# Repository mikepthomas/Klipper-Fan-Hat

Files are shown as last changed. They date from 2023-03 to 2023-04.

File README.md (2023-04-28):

# Klipper Fan Hat

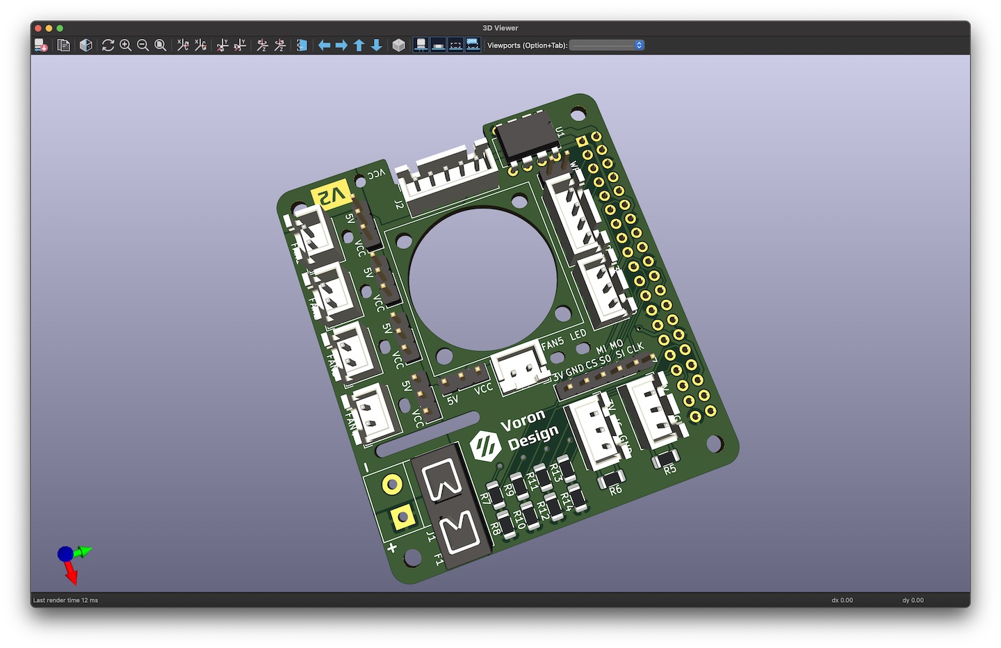
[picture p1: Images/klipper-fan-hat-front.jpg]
Klipper Fan Hat Front


[Interactive bom](https://mikethomas.info/Klipper-Fan-Hat)

### A Hat to use with the [Raspberry Pi as a Secondary MCU in Klipper](https://www.klipper3d.org/RPi_microcontroller.html):
- SKR Pico compatible input for powering the Pi and Serial communication
- 5 Mosfet outputs (with 2 pin JST-XH connectors standard on most fans used on 3D printers)
- Voltage selector jumpers to power each fan from either 5V or VCC supplied by screw terminal
- I2C and 1-Wire and SPI headers for connecting accesories to the Raspberry Pi
- 2 headers connected to General Purpose GPIO pins for accesories such as Filament Run Out Sensors

### Documentation

[Documentation and Setup information here](Documentation/README.md)

 Parts that I sourced for assembly:
- 1206 Capacitor Set [Ali Express](https://www.aliexpress.com/item/1005002907508304.html)
- 1206 LEDs [Ali Express](https://www.aliexpress.com/item/1005003836509392.html)
- 1206 Resistor Set [Ali Express](https://www.aliexpress.com/item/33029877427.html)
- 2510 Axial Fan [Ali Express](https://www.aliexpress.com/item/32807610078.html)
- Blade Fuse Holder [Ali Express](https://www.aliexpress.com/item/1005003194700697.html)
- DIP-8 24C32 EEPROM [Ali Express](https://www.aliexpress.com/item/33036366759.html)
- DIP-8 Socket [Ali Express](https://www.aliexpress.com/item/1005001650813894.html)
- IRLML6344TRPBF Mosfets [Ali Express](https://www.aliexpress.com/item/1005004711783484.html)
- JST-XH Connector Set [Ali Express](https://www.aliexpress.com/item/33000442968.html)
- Jumper Caps [Ali Express](https://www.aliexpress.com/item/1005004482029258.html)
- KF301 Screw Terminal [Ali Express](https://www.aliexpress.com/item/1005003311688833.html)
- M2.5x14 BHCS [Ali Express](https://www.aliexpress.com/item/1005004123548619.html)
- Pin Header Set [Amazon](https://www.amazon.co.uk/gp/product/B07CWSXY7P)
- Raspberry Pi Headers and Spacers [Amazon](https://www.amazon.co.uk/gp/product/B07PHBTTGV)

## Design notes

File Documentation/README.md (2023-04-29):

- [Components](#components)
  - [Indicator LEDs](#indicator-leds)
  - [Power In](#power-in)
  - [Serial Header](#serial-header)
  - [I2C Header](#i2c-header)
  - [1-wire Header](#1-wire-header)
  - [GPIO Header](#gpio-header)
  - [SPI Header](#spi-header)
  - [Fan Mosfets](#fan-mosfets)
- [Setup](#setup)

# Components

## Indicator LEDs

There are 7 status indicator LEDs on the board:

- Status LED to indicate that the board is communicating with Klipper (LED)
- VCC status indicates that there is power present on the Vin and GND feeding the board through the screw terminals (J1)
- 5 Fan Status LEDs to indicate if the Fan Mosfets have power applied to them (FAN1-FAN5)

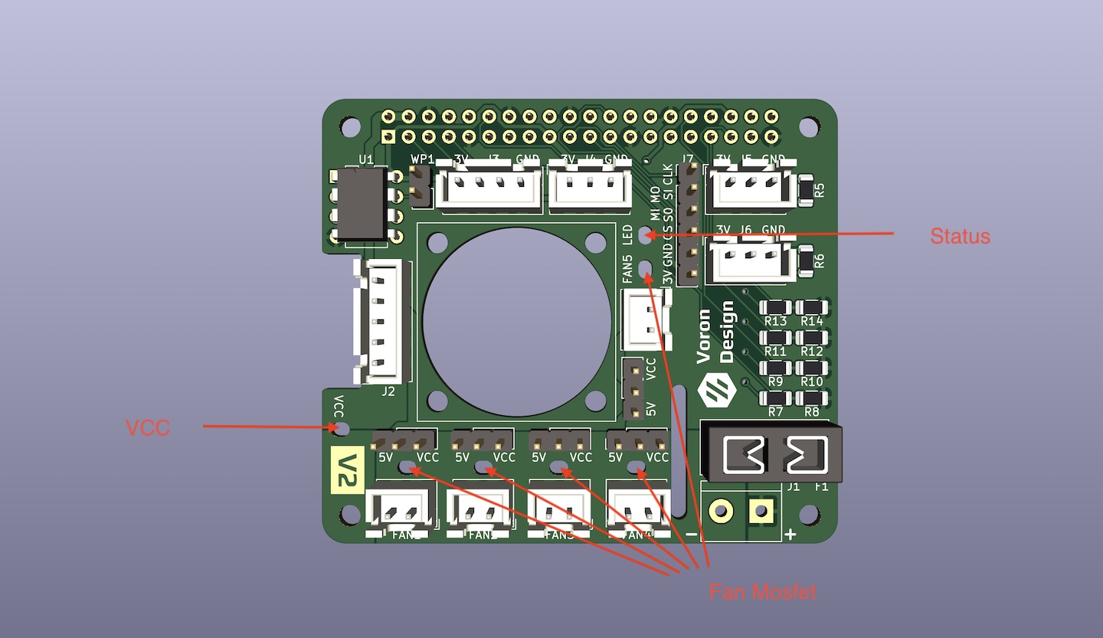
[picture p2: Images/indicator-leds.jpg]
Indicator LEDs


The Status LED is connected directly to GPIO16 with a current limiting resistor.

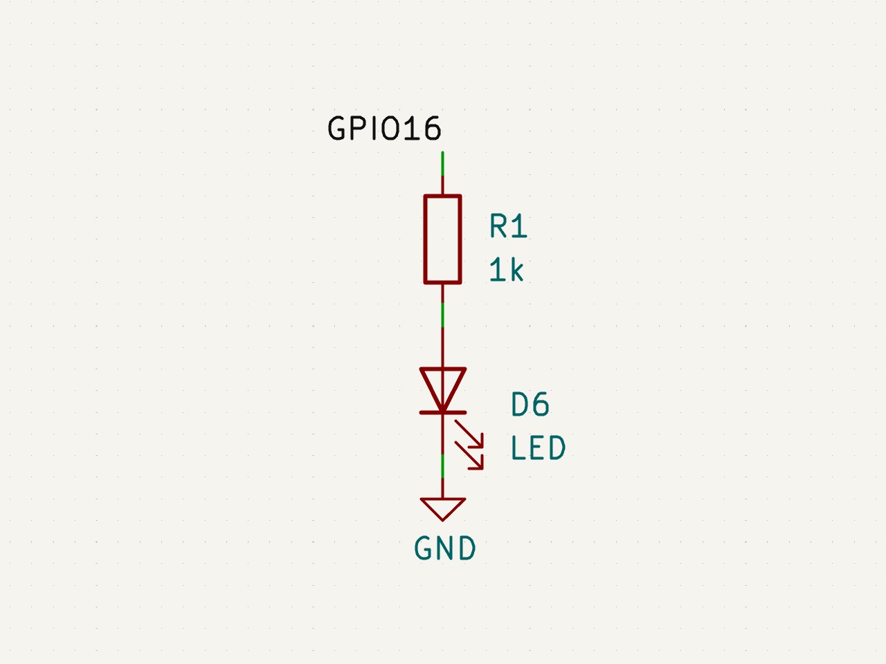
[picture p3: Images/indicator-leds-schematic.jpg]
Indicator LEDs Schematic


Example klipper ready status configuration:

```bash
[static_digital_output status_led]
pins: rpi:gpio16
```

## Power In

VCC and GND are for feeding power to the Mosfets, this would typically be either 12V or 24V.

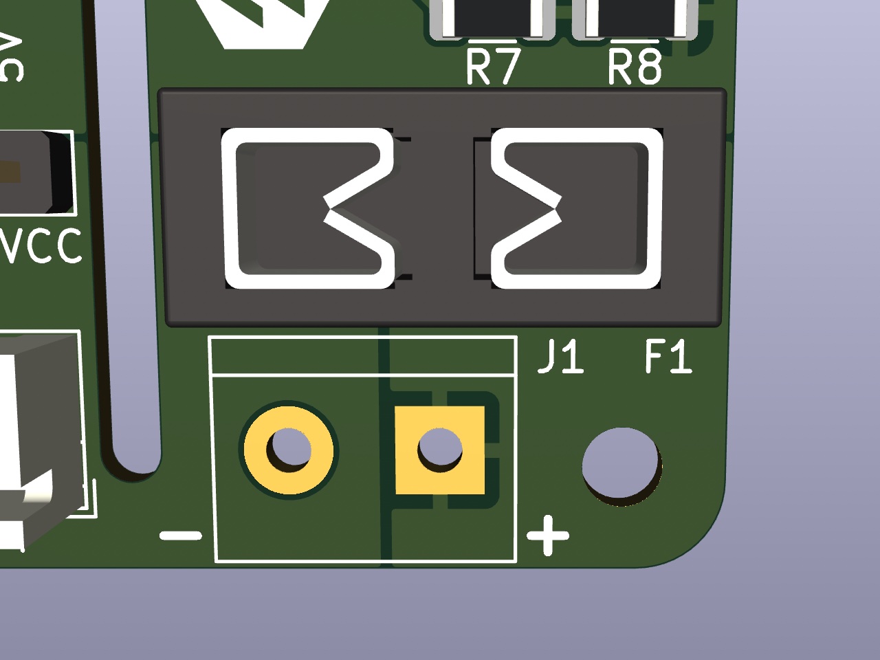
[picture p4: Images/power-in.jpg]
Power In


The fuse is a micro blade type fuse and should be chosen to the maximum draw of all of the MOSFET fed devices.

For example, if you are running a 40W heater, 2 5W fans and 1 2W fan, you will need a total of 62W of power. At 24V, this would translate to 62W/24V = 2.58A. The closest fuse might be a 5A fuse, which you should use.

Maximum power should not exceed 12A as the MOSFETs are each rated to a maximum of 3A.

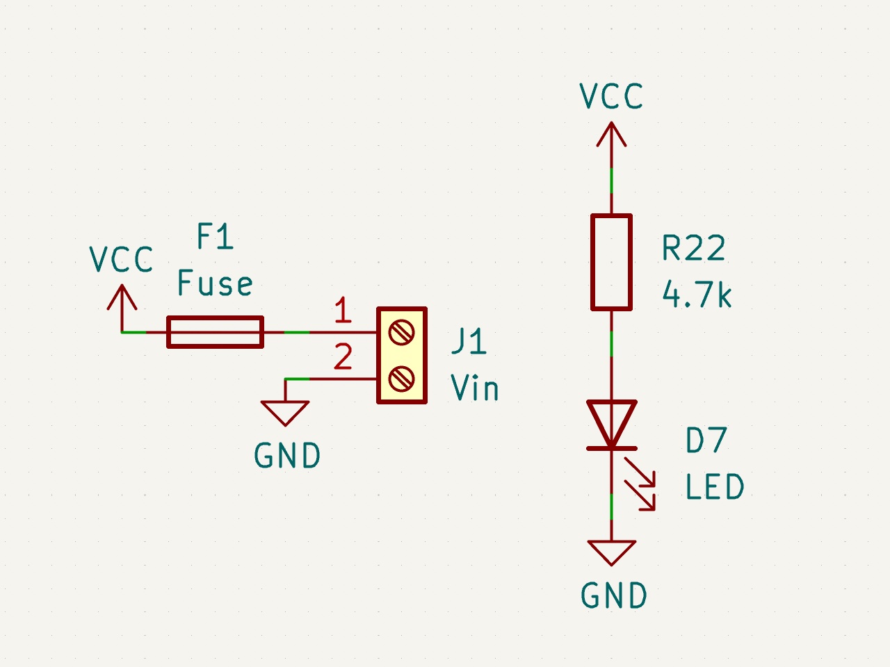
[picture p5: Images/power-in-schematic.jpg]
Power In Schematic


## Serial Header

SKR Pico compatible interface, can be used to both power the Raspberry Pi and communicate with the MCU over Serial.

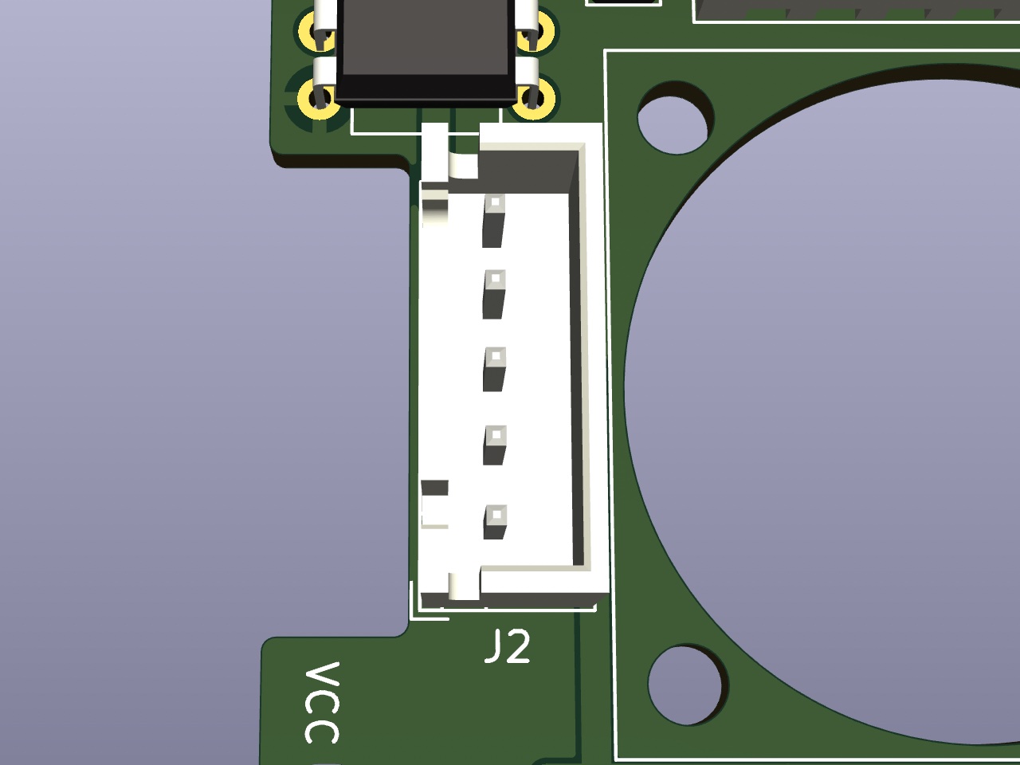
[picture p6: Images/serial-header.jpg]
Serial Header


The 5V pins are connected directly to the Raspberry Pi 5V pins and also supply 5V to the mosfet power selector headers.

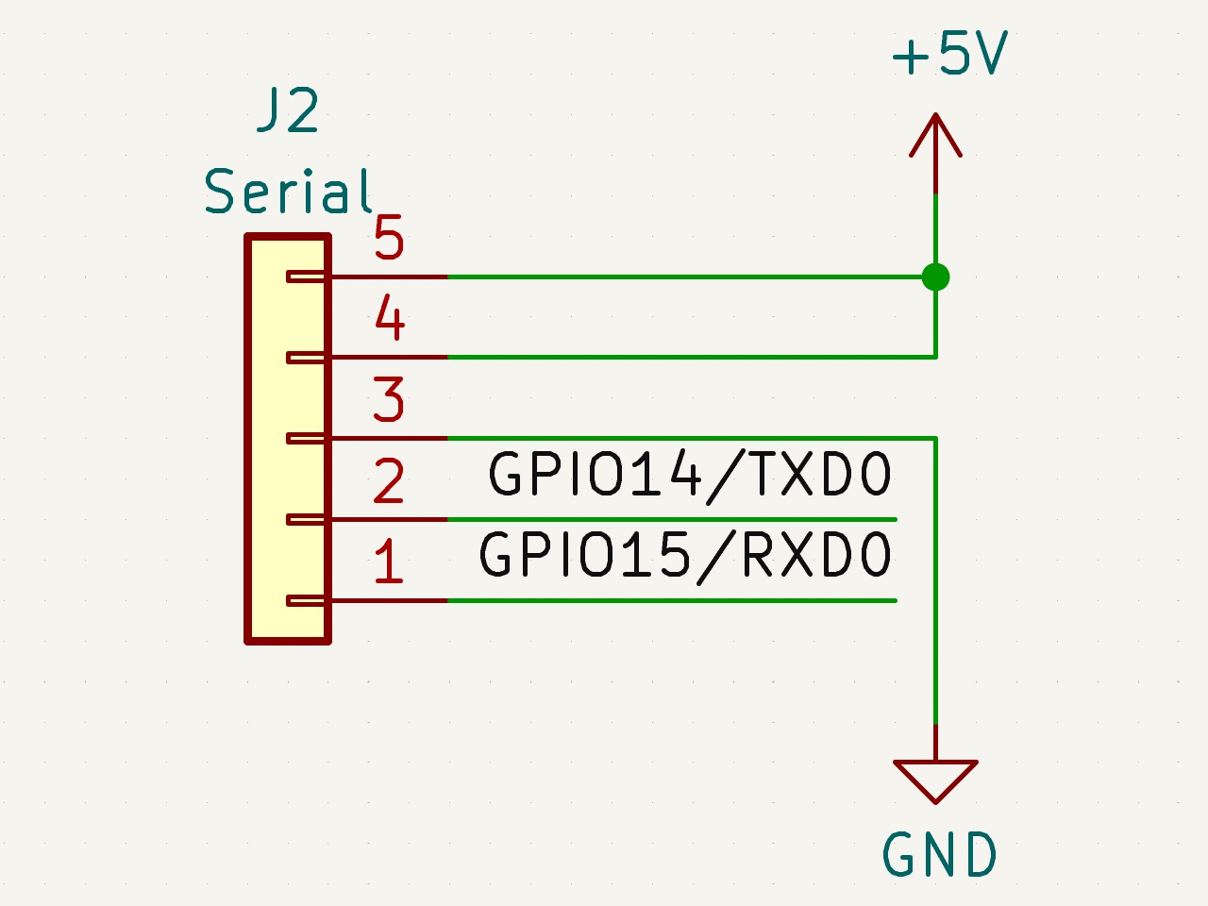
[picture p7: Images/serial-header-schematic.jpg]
Serial Header Schematic


## I2C Header

Contains a 3.3V I2C bus for connecting displays, and other sensors such as environemntal sensors and breakout expanders. This plugs into J3.

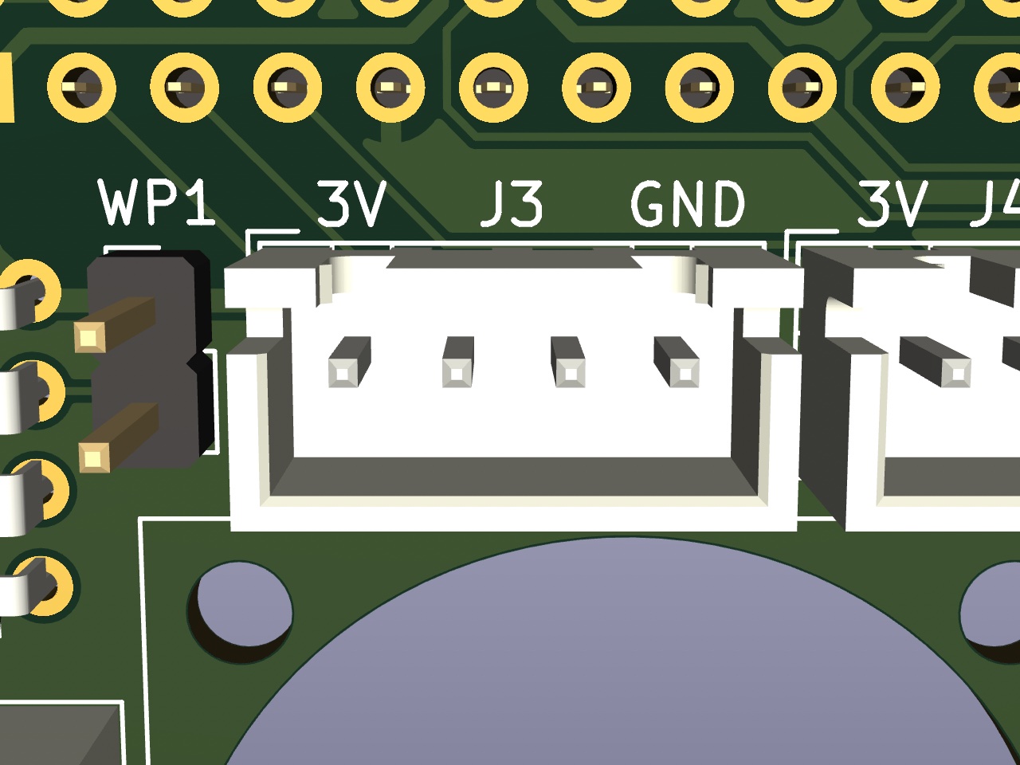
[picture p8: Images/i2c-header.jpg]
I2C Header


There are no Pull Up resistors on the I2C Bus as the Raspberry Pi already includes them.

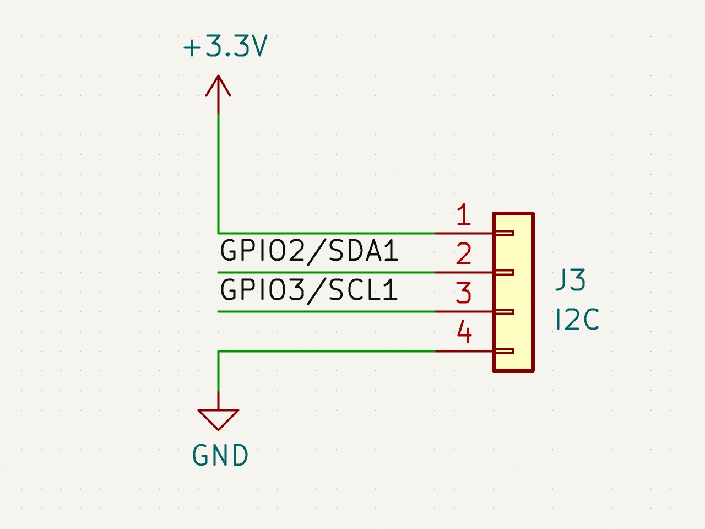
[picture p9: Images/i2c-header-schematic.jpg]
I2C Header Schematic


Example display configuration:

```bash
[display]
lcd_type: sh1106
i2c_mcu: rpi
i2c_bus: i2c.1
```

Example HTU21D temperature sensor configuration:

```bash
[temperature_sensor enclosure_temp]
sensor_type: HTU21D
i2c_mcu: rpi
i2c_bus: i2c.1

[gcode_macro QUERY_ENCLOSURE]
gcode:
    {% set sensor = printer["htu21d enclosure_temp"] %}
    {action_respond_info(
        "Temperature: %.2f C\n"
        "Humidity: %.2f%%" % (
            sensor.temperature,
            sensor.humidity))}
```

## 1-wire Header

The 1-wire connector can be used for connecting 1-wire sensors or can also be used as another generic GPIO Header.

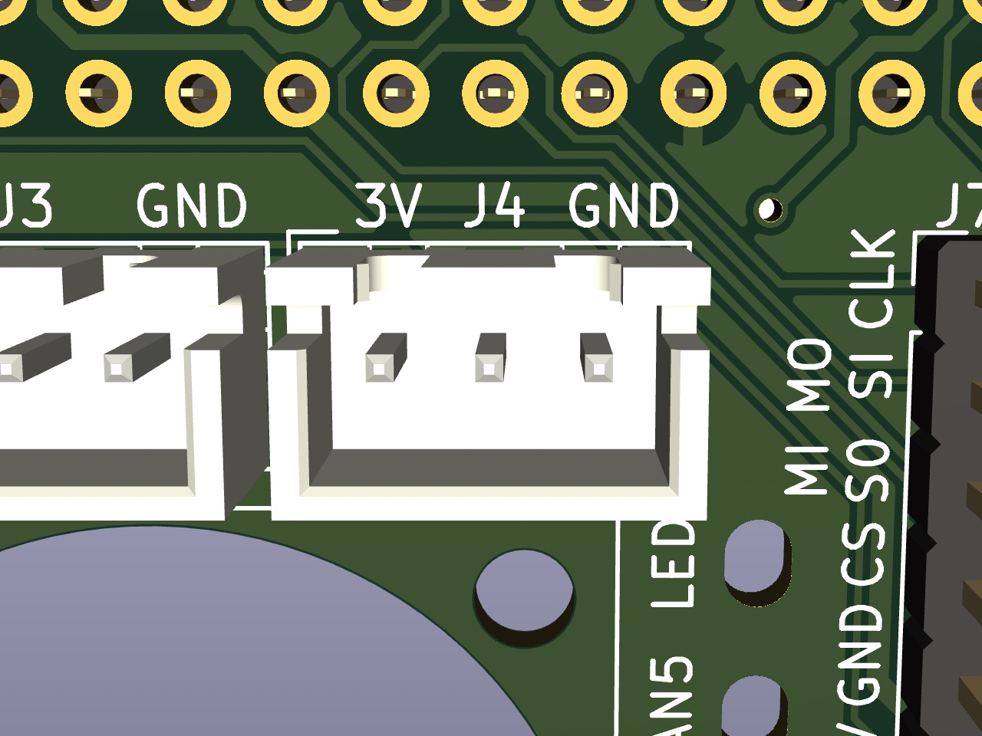
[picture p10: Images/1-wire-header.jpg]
1-wire Header


The 1-wire pin, GPIO4 is pulled up to 3V3 with a 3.9k resistor.

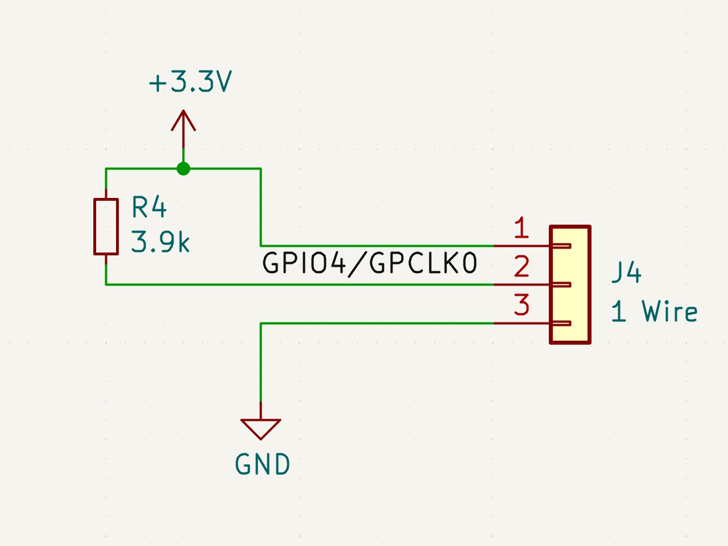
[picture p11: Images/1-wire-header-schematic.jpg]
1-wire Header Schematic


Example Output Pin configuration:

```bash
[output_pin gpio4]
pin: rpi:gpio4
value: 0
shutdown_value: 0
```

Example DS18B20 temperature sensor configuration:

```bash
[temperature_sensor enclosure_temp]
sensor_type: DS18B20
serial_no: 28-031674b175ff # Find with: ls /sys/bus/w1/devices/
ds18_report_time: 3.0 # Seconds between readings, minimum of 1.0
sensor_mcu: rpi
```

## GPIO Header

The GPIO headers J4 and J5 (3V3, GPIO, GND) is available for creative uses.

Examples of what this can be used for include adding external mosfets, relays or a filament runout sensors.

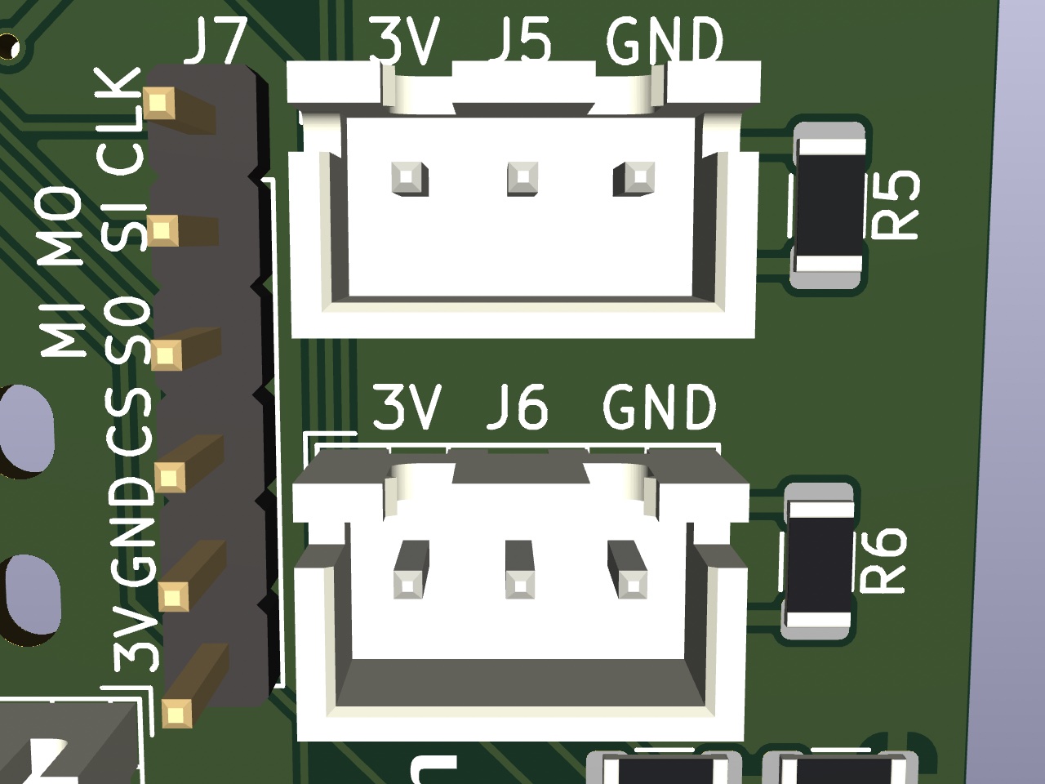
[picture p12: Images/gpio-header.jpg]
GPIO Header


Both GPIO5 and GPIO6 pins are pulled up to 3V3 with a 3.9k resistor.

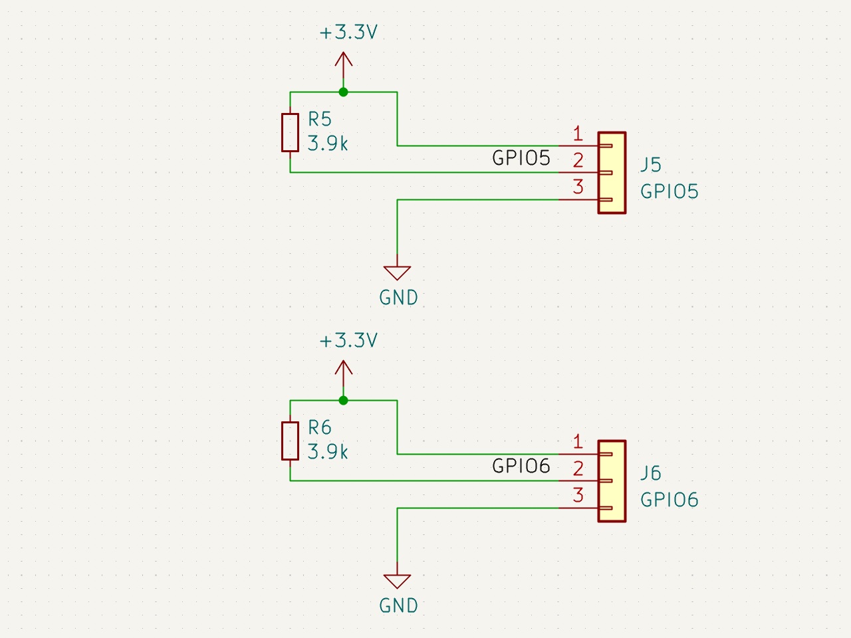
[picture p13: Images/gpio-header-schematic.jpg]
GPIO Header Schematic


Example Output Pin configuration:

```bash
[output_pin gpio5]
pin: rpi:gpio5
value: 0
shutdown_value: 0
```

Example Filament Sensor configuration:

```bash
[filament_switch_sensor filament_sensor]
pause_on_runout: true
switch_pin: ^!rpi:gpio5
```

## SPI Header

Contains a 3.3V SPI bus for connecting displays, and other sensors such as environmental sensors and breakout expanders. This plugs into J7.

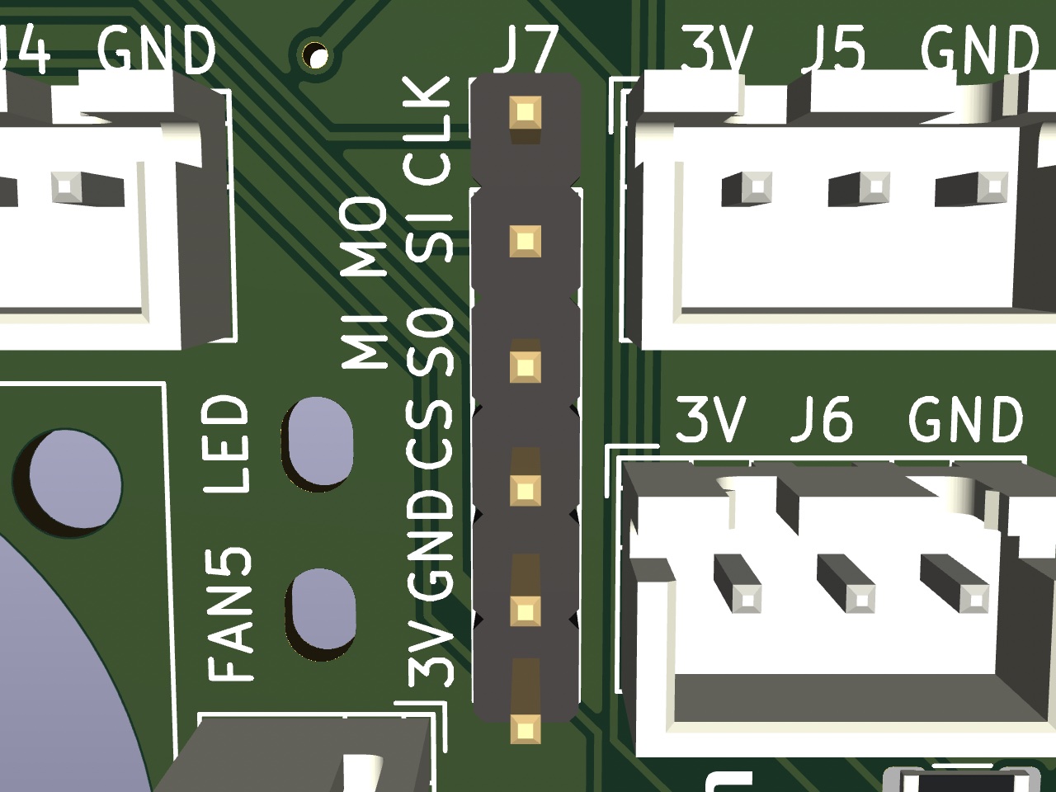
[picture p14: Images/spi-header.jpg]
SPI Header


This connects directly to the Raspberry Pi's SPI0 and uses CE0, CE1 is left unconnected.

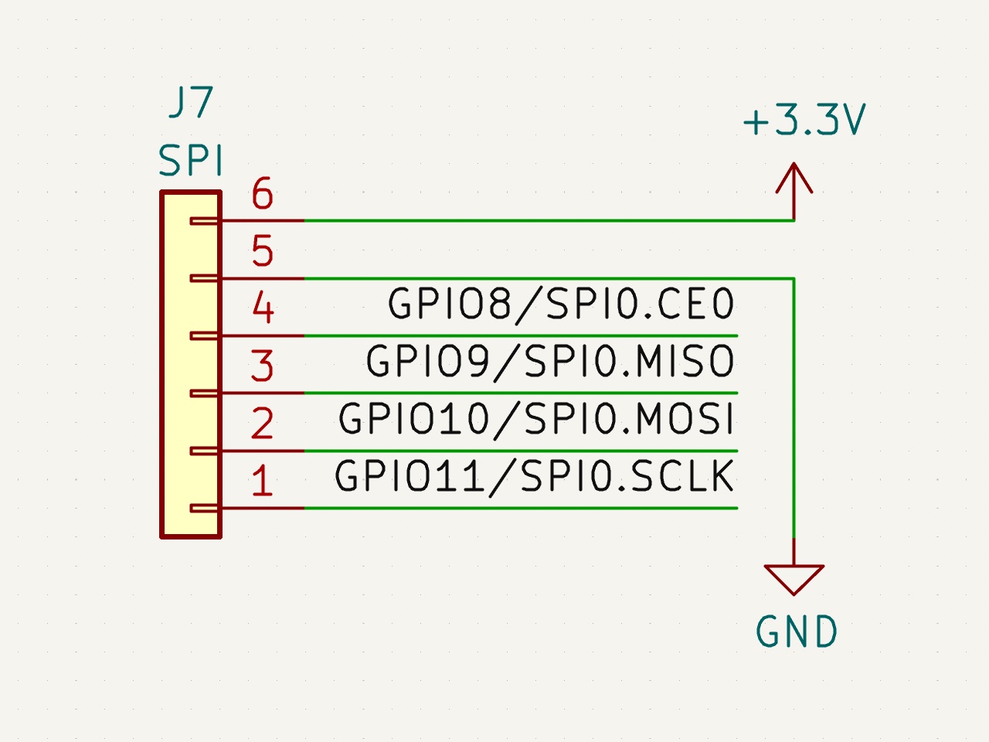
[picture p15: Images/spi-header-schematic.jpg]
SPI Header Schematic


Example AXDL345 configuration:

```bash
[adxl345]
cs_pin: rpi:None

[resonance_tester]
accel_chip: adxl345
probe_points: 150, 150, 20
```

## Fan Mosfets

5 x 3A mosfets for controlling LED's, Heater, Fans, and other accessories connected to pins GPIO12, GPIO13, GPIO17, GPIO18 and GPIO19.

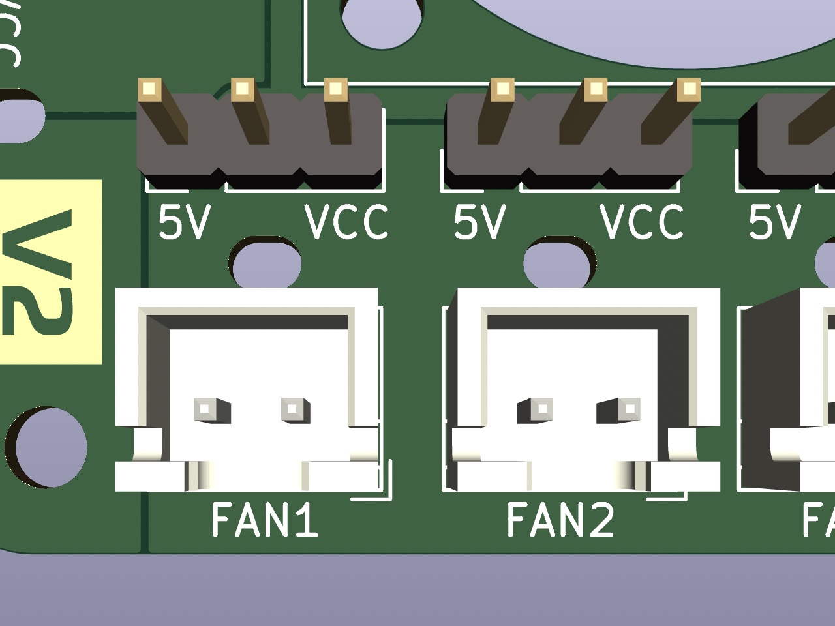
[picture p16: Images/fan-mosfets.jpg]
Fan Mosfets


The voltage selector header can be used to connect each mosfet to either the 5V rail or VCC.

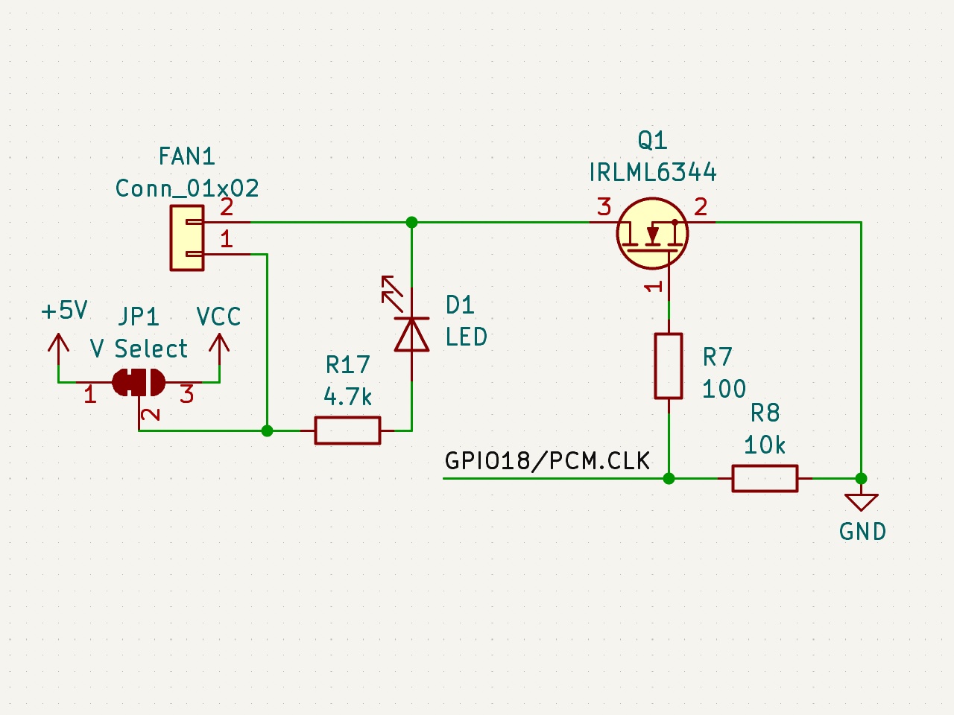
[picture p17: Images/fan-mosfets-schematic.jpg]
Fan Mosfets Schematic


Example Output Pin configuration:

```bash
[output_pin mosfet1]
pin: rpi:gpio18
value: 0
shutdown_value: 0
```

Example Fan configuration:

```bash
[fan_generic fan1]
pin: rpi:gpio18
```

Example Hardware PWM Fan configuration:

```bash
[fan_generic fan1]
pin: rpi:pwmchip0/pwm0
hardware_pwm: true
```

# Setup

If you purchased your board already assembled, it is likely that the hat EEPROM has already been flashed. However, if you are building it yourself you will need [Flash the EEPROM by following this guide](../EEPROM/README.md).

You should just be able to go through the [Klipper RPi micro-controller setup guide](https://www.klipper3d.org/RPi_microcontroller.html), and that page will be the most up-to-date with the latest Klipper version.

## Install the RC Script

If you want to use the host as a secondary MCU the klipper_mcu process must run before the klippy process.

After installing Klipper, install the script. run:

```bash
cd ~/klipper/
sudo cp ./scripts/klipper-mcu.service /etc/systemd/system/
sudo systemctl enable klipper-mcu.service
```

## Building the Micro-Controller Code

To compile the Klipper micro-controller code, start by configuring it for the `Linux process`:

```bash
cd ~/klipper/
make menuconfig
```

In the menu, set `Micro-controller Architecture` to `Linux process`, then save and exit.

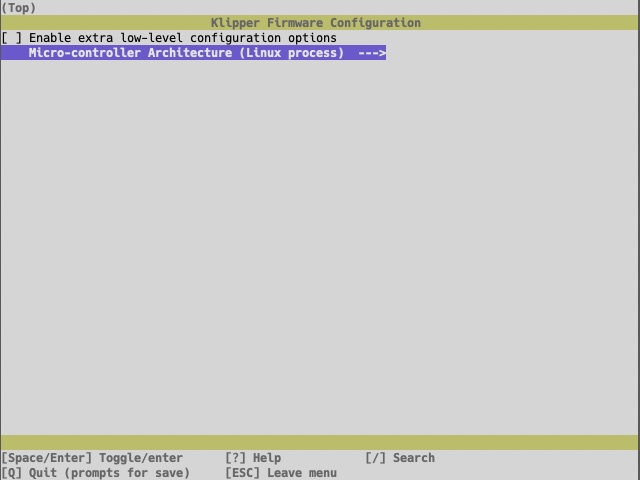
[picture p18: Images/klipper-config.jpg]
Klipper Config


To build and install the new micro-controller code, run:

```bash
sudo service klipper stop
make flash
sudo service klipper start
```

If klippy.log reports a `Permission denied` error when attempting to connect to `/tmp/klipper_host_mcu` then you need to add your user to the tty group. The following command will add the `pi` user to the `tty` group:

```bash
sudo usermod -a -G tty pi
```

## Remaining configuration

You can copy the config from the EEPROM chip of the hat into the Klipper config directory:

```bash
cat /proc/device-tree/hat/custom_1 > ~/printer_data/config/klipper-fan-hat.cfg
```

## Optional: Enabling SPI

SPI should be enabled automatically by the hat EEPROM, If you have trouble, you can enable it manually by running `sudo raspi-config` and enabling SPI under the `Interfacing options` menu.

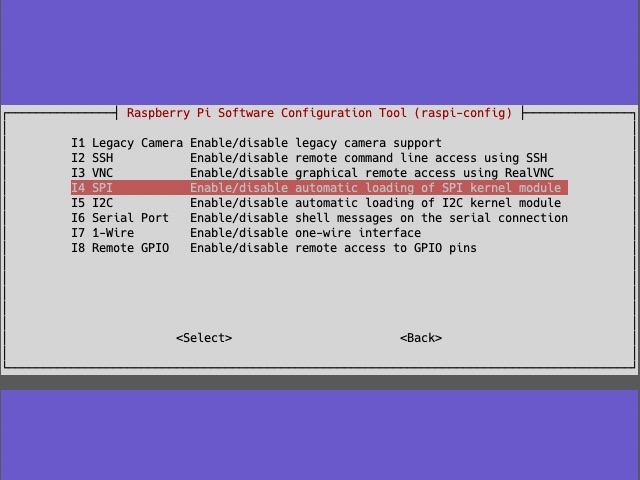
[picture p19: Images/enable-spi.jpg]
Enable SPI


## Optional: Enabling I2C

I2C should be enabled automatically by the hat EEPROM, If you have trouble, you can enable it manually by running `sudo raspi-config` and enabling I2C under the `Interfacing options` menu.

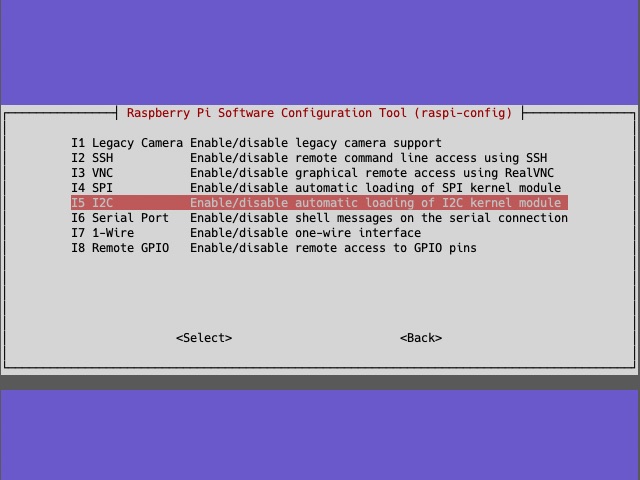
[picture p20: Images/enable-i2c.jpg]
Enable I2C


If planning to use I2C for the MPU accelerometer, it is also required to set the baud rate to 400000 by: adding/uncommenting `dtparam=i2c_arm=on,i2c_arm_baudrate=400000` in `/boot/config.txt` (or `/boot/firmware/config.txt` in some distros).
This should also be automatically be enabled by the hat EEPROM however you can do it manually if you have any problems.

## Optional: Enabling 1-wire

If you require, you can enable the 1-wire interface by running `sudo raspi-config` and enabling 1-wire under the `Interfacing options` menu.

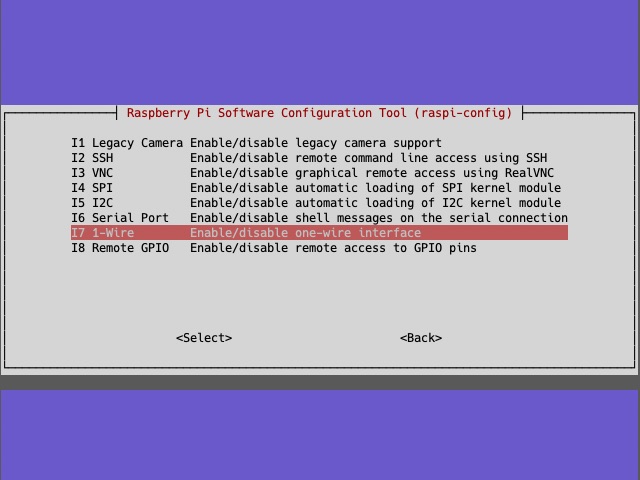
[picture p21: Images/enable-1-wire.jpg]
Enable 1-wire


you can then find any conneted sensors serial numbers with: `ls /sys/bus/w1/devices/`

## Optional: Hardware PWM

Raspberry Pi's have two PWM channels (PWM0 and PWM1) which are exposed on the header or if not, can be routed to existing gpio pins. The Linux mcu daemon uses the pwmchip sysfs interface to control hardware pwm devices on Linux hosts. The pwm sysfs interface is not exposed by default on a Raspberry and can be activated by adding a line to `/boot/config.txt`:

```bash
# Enable pwmchip sysfs interface
dtoverlay=pwm,pin=12,func=4
```

This example enables only PWM0 and routes it to gpio12. If both PWM channels need to be enabled you can use `pwm-2chan`:

```bash
# Enable pwmchip sysfs interface
dtoverlay=pwm-2chan,pin=12,pin2=13,func=4,func2=4
```

The overlay does not expose the pwm line on sysfs on boot and needs to be exported by echo'ing the number of the pwm channel to `/sys/class/pwm/pwmchip0/export`:

```bash
echo 0 > /sys/class/pwm/pwmchip0/export
```

If you have enabled `pwm-2chan` you can enable PWM1 too with:

```bash
echo 1 > /sys/class/pwm/pwmchip0/export
```

This will create device `/sys/class/pwm/pwmchip0/pwm0` and optionally `/sys/class/pwm/pwmchip0/pwm1` in the filesystem. The easiest way to do this is by adding them to `/etc/rc.local` before the `exit 0` line.

With the sysfs in place, you can now use either the pwm channel(s) by adding the following piece of configuration to your `klipper-fan-hat.cfg`:

```bash
[fan_generic fan1]
pin: rpi:pwmchip0/pwm0
hardware_pwm: true
cycle_time: 0.000001
```

This will add hardware pwm control to gpio12 on the Pi (because the overlay was configured to route pwm0 to pin=12).

PWM0 can be routed to gpio12 and gpio18, PWM1 can be routed to gpio13 and gpio19:

| PWM | gpio PIN | Func |
| --- | --- | ---- |
| 0 | 12 | 4 |
| 0 | 18 | 2 |
| 1 | 13 | 4 |
| 1 | 19 | 2 |

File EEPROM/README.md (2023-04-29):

# Flashing Hat EEPROM

## Connect EEPROM

The Raspberry Pi should be powered off before making any connections to the GPIO pins.

The hat is wired to connect the EEPROM to the Raspberry Pi's ID pins with the required pull up resistors.

Connect the hat to the Pi, remove the jumper from the WP1 header and switch on the Raspberry Pi.

## Install required tools

We will need to install some tools that are not included in the base Raspberry Pi OS image, at the command prompt:

```bash
pi@raspberrypi:~ $ sudo apt update
pi@raspberrypi:~ $ sudo apt install device-tree-compiler git i2c-tools -y
```

## Test EEPROM is Connected

Run the following command as explained in the [EEPROM Utils Docs](https://github.com/raspberrypi/hats/tree/master/eepromutils).

```bash
pi@raspberrypi:~ $ sudo dtoverlay i2c-gpio i2c_gpio_sda=0 i2c_gpio_scl=1 bus=9
pi@raspberrypi:~ $ i2cdetect -y 9
```

You should then be able to see the EEPROM Chip at address 50:

```bash
     0  1  2  3  4  5  6  7  8  9  a  b  c  d  e  f
00:                         -- -- -- -- -- -- -- --
10: -- -- -- -- -- -- -- -- -- -- -- -- -- -- -- --
20: -- -- -- -- -- -- -- -- -- -- -- -- -- -- -- --
30: -- -- -- -- -- -- -- -- -- -- -- -- -- -- -- --
40: -- -- -- -- -- -- -- -- -- -- -- -- -- -- -- --
50: 50 -- -- -- -- -- -- -- -- -- -- -- -- -- -- --
60: -- -- -- -- -- -- -- -- -- -- -- -- -- -- -- --
70: -- -- -- -- -- -- -- --
```

## Clone Hats Git Repository

Next we need to get the code from the Raspberry Pi Hats Repository.

```bash
pi@raspberrypi:~ $ git clone https://github.com/raspberrypi/hats.git
```

Once we have cloned the repository we need to compile the tools to make the EEPROM image.

```bash
pi@raspberrypi:~ $ cd hats/eepromutils/
pi@raspberrypi:~/hats/eepromutils $ make -j4
```

## Get the required Files

We need 3 files to configure the EEPROM flash file:

- eeprom_settings.txt - [the Klipper Fan Hat EEPROM settings file](https://github.com/mikepthomas/Klipper-Fan-Hat/blob/main/EEPROM/eeprom_settings.txt)
- klipper-fan-hat.dts - [the Klipper Fan Hat device tree source file](https://github.com/mikepthomas/Klipper-Fan-Hat/blob/main/EEPROM/klipper-fan-hat.dts)
- klipper-fan-hat.cfg - [the Klipper config source file](https://github.com/mikepthomas/Klipper-Fan-Hat/blob/main/Software/klipper-fan-hat.cfg)

Save these into the `~/hats/eepromutils` directory

To allow the hat to automatically enable I2C and SPI compile the binary and set the correct permissions to the output file:

```bash
pi@raspberrypi:~/hats/eepromutils $ sudo dtc -@ -I dts -O dtb -o klipper-fan-hat.dtb klipper-fan-hat.dts
pi@raspberrypi:~/hats/eepromutils $ sudo chown pi:pi klipper-fan-hat.dtb
```

## Zero EEPROM

The Recommended EEPROM in the [Design Guide](https://github.com/raspberrypi/hats/blob/master/designguide.md) at the time of writing is CAT24C32 which is 32kbit (4kbyte).

As we don't know the state of the EEPROM it is best to clear it by setting it all to zeros.
If your EEPROM is a different size you will need to set `count` to the value of kbyte of your chip.

Make a blank image using dd...

```bash
pi@raspberrypi:~/hats/eepromutils $ dd if=/dev/zero ibs=1k count=4 of=blank.eep
```

...and flash it to the chip.

```bash
pi@raspberrypi:~/hats/eepromutils $ sudo ./eepflash.sh -w -f=blank.eep -t=24c32
```

## Flash EEPROM

Now that we have a blank EEPROM chip, We can can configure the hat EEPROM image and embed the device tree binary & klipper config into the flash file.

```bash
pi@raspberrypi:~/hats/eepromutils $ ./eepmake eeprom_settings.txt klipper-fan-hat.eep klipper-fan-hat.dtb -c klipper-fan-hat.cfg
```

...then flash it to the EEPROM chip.

```bash
pi@raspberrypi:~/hats/eepromutils $ sudo ./eepflash.sh -w -f=klipper-fan-hat.eep -t=24c32
```

## Test EEPROM

The Hat EEPROM is read on system boot so we will need to reboot the Pi before we can test it:

```bash
pi@raspberrypi:~/hats/eepromutils $ sudo reboot
```

Log back in and you will be able to see the devices `/dev/i2c-1`, and `/dev/spidev0.0` and `/dev/spidev0.1` only when the hat EEPROM is connected.

```bash
pi@raspberrypi:~ $ ls /dev
autofs         dma_heap   i2c-1    loop4         mmcblk0    ram1   ram5     spidev0.0  tty12  tty21  tty30  tty4   tty49  tty58  ttyAMA0    vcs1   vcsa4     vcsu6    video20
block          dri        i2c-2    loop5         mmcblk0p1  ram10  ram6     spidev0.1  tty13  tty22  tty31  tty40  tty5   tty59  ttyprintk  vcs2   vcsa5     vhci     video21
btrfs-control  fd         initctl  loop6         mmcblk0p2  ram11  ram7     stderr     tty14  tty23  tty32  tty41  tty50  tty6   uhid       vcs3   vcsa6     video10  video22
bus            full       input    loop7         mqueue     ram12  ram8     stdin      tty15  tty24  tty33  tty42  tty51  tty60  uinput     vcs4   vcsm-cma  video11  video23
cachefiles     fuse       kmsg     loop-control  net        ram13  ram9     stdout     tty16  tty25  tty34  tty43  tty52  tty61  urandom    vcs5   vcsu      video12  video31
cec0           gpiochip0  log      mapper        null       ram14  random   tty        tty17  tty26  tty35  tty44  tty53  tty62  v4l        vcs6   vcsu1     video13  watchdog
char           gpiochip1  loop0    media0        ppp        ram15  rfkill   tty0       tty18  tty27  tty36  tty45  tty54  tty63  vchiq      vcsa   vcsu2     video14  watchdog0
console        gpiochip2  loop1    media1        ptmx       ram2   serial1  tty1       tty19  tty28  tty37  tty46  tty55  tty7   vcio       vcsa1  vcsu3     video15  zero
cuse           gpiomem    loop2    media2        pts        ram3   shm      tty10      tty2   tty29  tty38  tty47  tty56  tty8   vc-mem     vcsa2  vcsu4     video16
disk           hwrng      loop3    mem           ram0       ram4   snd      tty11      tty20  tty3   tty39  tty48  tty57  tty9   vcs        vcsa3  vcsu5     video18
```

We can then read the data using the device tree...

```bash
pi@raspberrypi:~ $ cd /proc/device-tree/hat/
pi@raspberrypi:/proc/device-tree/hat $ ls
custom_0  custom_1  name  product  product_id  product_ver  uuid  vendor
pi@raspberrypi:/proc/device-tree/hat $ more name
hat
pi@raspberrypi:/proc/device-tree/hat $ more vendor
Voron Design
pi@raspberrypi:/proc/device-tree/hat $ more product
Klipper Fan Hat
pi@raspberrypi:/proc/device-tree/hat $ more product_id
0x4b46
pi@raspberrypi:/proc/device-tree/hat $ more product_ver
0x0002
pi@raspberrypi:/proc/device-tree/hat $ more uuid
fef562f0-9e28-4453-88c2-c073303e6ab2
```

...and also copy the config out of the device tree into the klipper config directory.

```bash
cat /proc/device-tree/hat/custom_1 > ~/printer_data/config/klipper-fan-hat.cfg
```

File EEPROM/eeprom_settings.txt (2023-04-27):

########################################################################
# EEPROM settings text file
#
# Edit this file for your particular board and run through eepmake tool,
# then use eepflash tool to write to attached HAT ID EEPROM
#
# Tools available:
#  eepmake   Parses EEPROM text file and creates binary .eep file
#  eepdump   Dumps a binary .eep file as human readable text (for debug)
#  eepflash  Write or read .eep binary image to/from HAT EEPROM
#
########################################################################

########################################################################
# Vendor info

# 128 bit UUID. If left at zero eepmake tool will auto-generate
# RFC 4122 compliant UUID
product_uuid 00000000-0000-0000-0000-000000000000

# 16 bit product id (KF in hex encoded ASCII)
product_id 0x4B46

# 16 bit product version
product_ver 0x0002

# ASCII vendor string  (max 255 characters)
vendor "Voron Design"

# ASCII product string (max 255 characters)
product "Klipper Fan Hat"

# Custom binary data
custom_data
57 65 20 62 75 69 6C 64 20 73 70 61 63 65 20 73 68 75 74 74 6C 65 73 20
77 69 74 68 20 67 61 72 64 65 6E 69 6E 67 20 74 6F 6F 6C 73 20 73 6F 20
61 6E 79 6F 6E 65 20 63 61 6E 20 68 61 76 65 20 61 20 73 70 61 63 65 20
73 68 75 74 74 6C 65 20 6F 66 20 74 68 65 69 72 20 6F 77 6E 2E 0A
end

########################################################################
# GPIO bank settings, set to nonzero to change from the default.
# NOTE these setting can only be set per BANK, uncommenting any of
# these will force the bank to use the custom setting.

# drive strength, 0=default, 1-8=2,4,6,8,10,12,14,16mA, 9-15=reserved
gpio_drive 0

# 0=default, 1=slew rate limiting, 2=no slew limiting, 3=reserved
gpio_slew 0

# 0=default, 1=hysteresis disabled, 2=hysteresis enabled, 3=reserved
gpio_hysteresis 0

# If board back-powers Pi via 5V GPIO header pins:
# 0 = board does not back-power
# 1 = board back-powers and can supply the Pi with a minimum of 1.3A
# 2 = board back-powers and can supply the Pi with a minimum of 2A
# 3 = reserved
# If back_power=2 then USB high current mode will be automatically
# enabled on the Pi
back_power 2

########################################################################
# GPIO pins, uncomment for GPIOs used on board
# Options for FUNCTION: INPUT, OUTPUT, ALT0-ALT5
# Options for PULL: DEFAULT, UP, DOWN, NONE
# NB GPIO0 and GPIO1 are reserved for ID EEPROM so cannot be set

#         GPIO  FUNCTION  PULL
#         ----  --------  ----
#setgpio  2     INPUT     DEFAULT   # J3 (I2C SDA1)
#setgpio  3     INPUT     DEFAULT   # J3 (I2C SCL1)
setgpio   4     INPUT     DEFAULT   # J4 (1-wire)
setgpio   5     INPUT     DEFAULT   # J5
setgpio   6     INPUT     DEFAULT   # J6
#setgpio  7     INPUT     DEFAULT   # Not Connected (SPI CE1)
#setgpio  8     INPUT     DEFAULT   # J7 (SPI CE0)
#setgpio  9     INPUT     DEFAULT   # J7 (SPI MISO)
#setgpio  10    INPUT     DEFAULT   # J7 (SPI MOSI)
#setgpio  11    INPUT     DEFAULT   # J7 (SPI SCLK)
#setgpio  12    OUTPUT    DEFAULT   # FAN2 (Cannot enable hardware PWM if set)
#setgpio  13    OUTPUT    DEFAULT   # FAN4 (Cannot enable hardware PWM if set)
#setgpio  14    INPUT     DEFAULT   # J2 (Serial TX)
#setgpio  15    INPUT     DEFAULT   # J2 (Serial RX)
setgpio   16    OUTPUT    DEFAULT   # Status LED
setgpio   17    OUTPUT    DEFAULT   # FAN5 (Pi Cooling Fan)
#setgpio  18    OUTPUT    DEFAULT   # FAN1 (Cannot enable hardware PWM if set)
#setgpio  19    OUTPUT    DEFAULT   # FAN3 (Cannot enable hardware PWM if set)
#setgpio  20    INPUT     DEFAULT   # Not Connected
#setgpio  21    INPUT     DEFAULT   # Not Connected
#setgpio  22    INPUT     DEFAULT   # Not Connected
#setgpio  23    INPUT     DEFAULT   # Not Connected
#setgpio  24    INPUT     DEFAULT   # Not Connected
#setgpio  25    INPUT     DEFAULT   # Not Connected
#setgpio  26    INPUT     DEFAULT   # Not Connected
#setgpio  27    INPUT     DEFAULT   # Not Connected

########################################################################
# Settings for bank 1 (only valid for CM1/3/3+/4S). Setting one or more of
# these GPIOs requires setting of drive, slew and hysteresis for bank 1.

# bank1_gpio_drive 0
# bank1_gpio_slew 0
# bank1_gpio_hysteresis 0

#setgpio  28    INPUT     DEFAULT
#setgpio  29    INPUT     DEFAULT
#setgpio  30    INPUT     DEFAULT
#setgpio  31    INPUT     DEFAULT
#setgpio  32    INPUT     DEFAULT
#setgpio  33    INPUT     DEFAULT
#setgpio  34    INPUT     DEFAULT
#setgpio  35    INPUT     DEFAULT
#setgpio  36    INPUT     DEFAULT
#setgpio  37    INPUT     DEFAULT
#setgpio  38    INPUT     DEFAULT
#setgpio  39    INPUT     DEFAULT
#setgpio  40    INPUT     DEFAULT
#setgpio  41    INPUT     DEFAULT
#setgpio  42    INPUT     DEFAULT
#setgpio  43    INPUT     DEFAULT
#setgpio  44    INPUT     DEFAULT
#setgpio  45    INPUT     DEFAULT

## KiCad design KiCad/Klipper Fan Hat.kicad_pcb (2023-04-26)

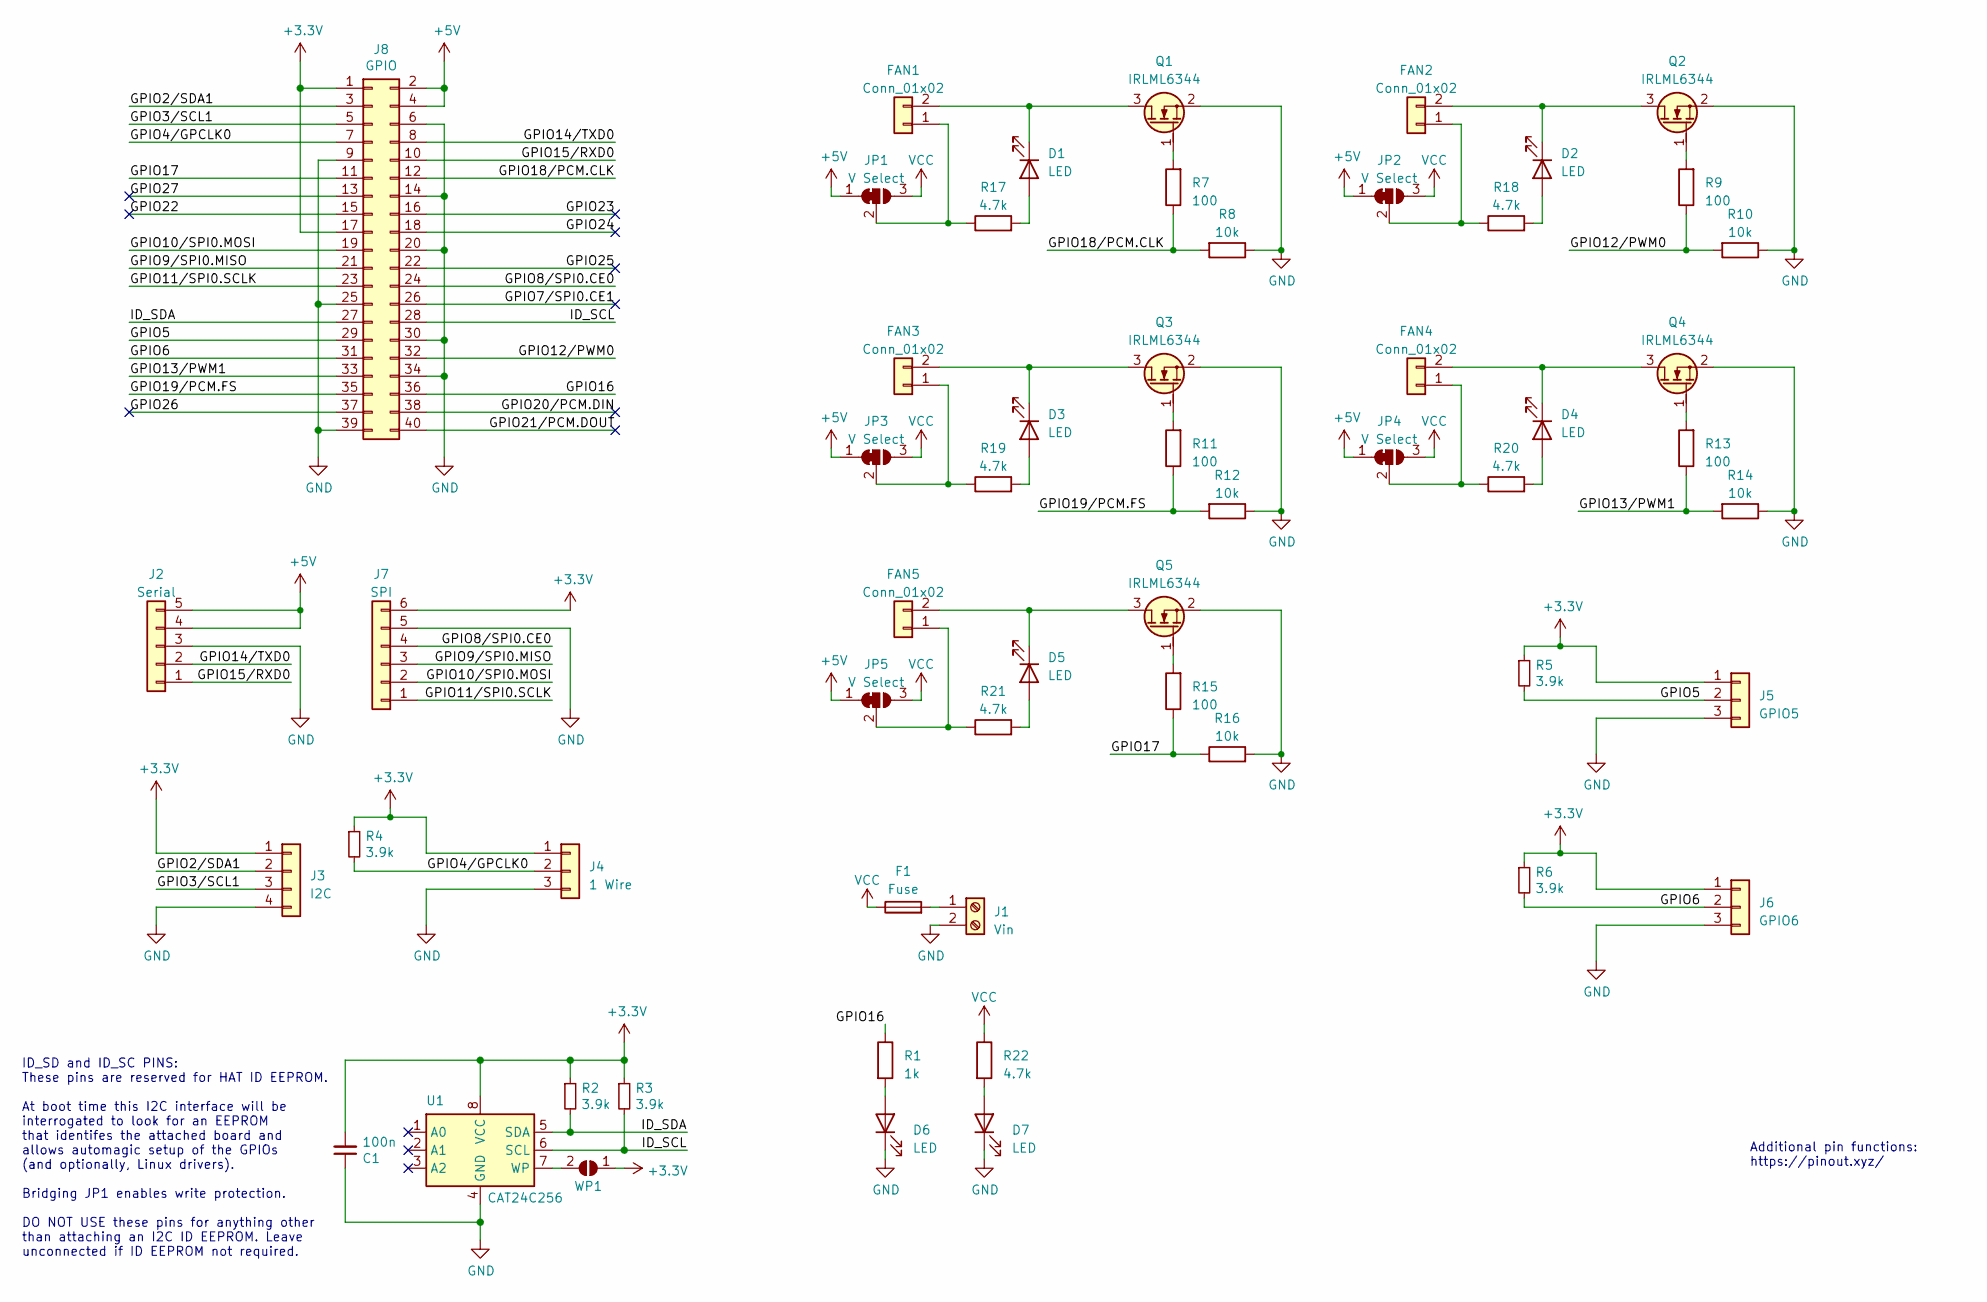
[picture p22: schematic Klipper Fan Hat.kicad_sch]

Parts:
C1: 100n; C_1206_3216Metric
D1, D2, D3, D4, D5, D6, D7: LED; LED_1206_3216Metric_ReverseMount_Hole1.8x2.4mm
F1: Fuse; Fuseholder_Blade_Mini_Keystone_3568
FAN1, FAN2, FAN3, FAN4, FAN5: Conn_01x02; JST_XH_B2B-XH-A_1x02_P2.50mm_Vertical
J1: Vin; TerminalBlock_bornier-2_P5.08mm
J2: Serial; JST_XH_B5B-XH-A_1x05_P2.50mm_Vertical
J3: I2C; JST_XH_B4B-XH-A_1x04_P2.50mm_Vertical
J4: 1 Wire; JST_XH_B3B-XH-A_1x03_P2.50mm_Vertical
J5: GPIO5; JST_XH_B3B-XH-A_1x03_P2.50mm_Vertical
J6: GPIO6; JST_XH_B3B-XH-A_1x03_P2.50mm_Vertical
J7: SPI; PinHeader_1x06_P2.54mm_Vertical
J8: GPIO; PinSocket_2x20_P2.54mm_Vertical
JP1, JP2, JP3, JP4, JP5: V Select; PinHeader_1x03_P2.54mm_Vertical
Q1, Q2, Q3, Q4, Q5: IRLML6344; TSOT-23
R1: 1k; R_1206_3216Metric
R2, R3, R4, R5, R6: 3.9k; R_1206_3216Metric
R7, R9, R11, R13, R15: 100; R_1206_3216Metric
R8, R10, R12, R14, R16: 10k; R_1206_3216Metric
R17, R18, R19, R20, R21, R22: 4.7k; R_1206_3216Metric
U1: CAT24C256; DIP-8_W7.62mm
WP1: ID_WP; PinHeader_1x02_P2.54mm_Vertical

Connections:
+3V3: C1.2, J3.1, J4.1, J5.1, J6.1, J7.6, J8.1, J8.17, R2.1, R3.1, R4.1, R5.1, R6.1, U1.8 (VCC), WP1.1 (A)
+5V: J2.4, J2.5, J8.2, J8.4, JP1.1 (A), JP2.1 (A), JP3.1 (A), JP4.1 (A), JP5.1 (A)
/GPIO2/SDA1: J3.2, J8.3
/GPIO3/SCL1: J3.3, J8.5
/GPIO4/GPCLK0: J4.2, J8.7, R4.2
/GPIO5: J5.2, J8.29, R5.2
/GPIO6: J6.2, J8.31, R6.2
/GPIO7/SPI0.CE1: J8.26
/GPIO8/SPI0.CE0: J7.4, J8.24
/GPIO9/SPI0.MISO: J7.3, J8.21
/GPIO10/SPI0.MOSI: J7.2, J8.19
/GPIO11/SPI0.SCLK: J7.1, J8.23
/GPIO12/PWM0: J8.32, R9.1, R10.2
/GPIO13/PWM1: J8.33, R13.1, R14.2
/GPIO14/TXD0: J2.2, J8.8
/GPIO15/RXD0: J2.1, J8.10
/GPIO16: J8.36, R1.1
/GPIO17: J8.11, R15.1, R16.1
/GPIO18/PCM.CLK: J8.12, R7.1, R8.2
/GPIO19/PCM.FS: J8.35, R11.1, R12.2
/GPIO20/PCM.DIN: J8.38
/GPIO21/PCM.DOUT: J8.40
/GPIO22: J8.15
/GPIO23: J8.16
/GPIO24: J8.18
/GPIO25: J8.22
/GPIO26: J8.37
/GPIO27: J8.13
/ID_SCL: J8.28, R3.2, U1.6 (SCL)
/ID_SDA: J8.27, R2.2, U1.5 (SDA)
GND: C1.1, D6.1 (K), D7.1 (K), J1.2, J2.3, J3.4, J4.3, J5.3, J6.3, J7.5, J8.6, J8.9, J8.14, J8.20, J8.25, J8.30, J8.34, J8.39, Q1.2 (S), Q2.2 (S), Q3.2 (S), Q4.2 (S), Q5.2 (S), R8.1, R10.1, R12.1, R14.1, R16.2, U1.4 (GND)
unnamed: D1.2 (A), R17.2
unnamed: D1.1 (K), FAN1.2, Q1.3 (D)
unnamed: D2.2 (A), R18.2
unnamed: D2.1 (K), FAN2.2, Q2.3 (D)
unnamed: D3.2 (A), R19.2
unnamed: D3.1 (K), FAN3.2, Q3.3 (D)
unnamed: D4.2 (A), R20.2
unnamed: D4.1 (K), FAN4.2, Q4.3 (D)
unnamed: D5.2 (A), R21.2
unnamed: D5.1 (K), FAN5.2, Q5.3 (D)
unnamed: D6.2 (A), R1.2
unnamed: D7.2 (A), R22.2
unnamed: FAN1.1, JP1.2 (C), R17.1
unnamed: FAN2.1, JP2.2 (C), R18.1
unnamed: FAN3.1, JP3.2 (C), R19.1
unnamed: FAN4.1, JP4.2 (C), R20.1
unnamed: FAN5.1, JP5.2 (C), R21.1
unnamed: F1.2, J1.1
unnamed: Q1.1 (G), R7.2
unnamed: Q2.1 (G), R9.2
unnamed: Q3.1 (G), R11.2
unnamed: Q4.1 (G), R13.2
unnamed: Q5.1 (G), R15.2
unnamed: U1.7 (WP), WP1.2 (B)
VCC: F1.1, JP1.3 (B), JP2.3 (B), JP3.3 (B), JP4.3 (B), JP5.3 (B), R22.1

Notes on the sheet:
Additional pin functions: https://pinout.xyz/
ID_SD and ID_SC PINS: These pins are reserved for HAT ID EEPROM. At boot time this I2C interface will be interrogated to look for an EEPROM that identifes the attached board and allows automagic setup of the GPIOs (and optionally, Linux drivers). Bridging JP1 enables write protection. DO NOT USE th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

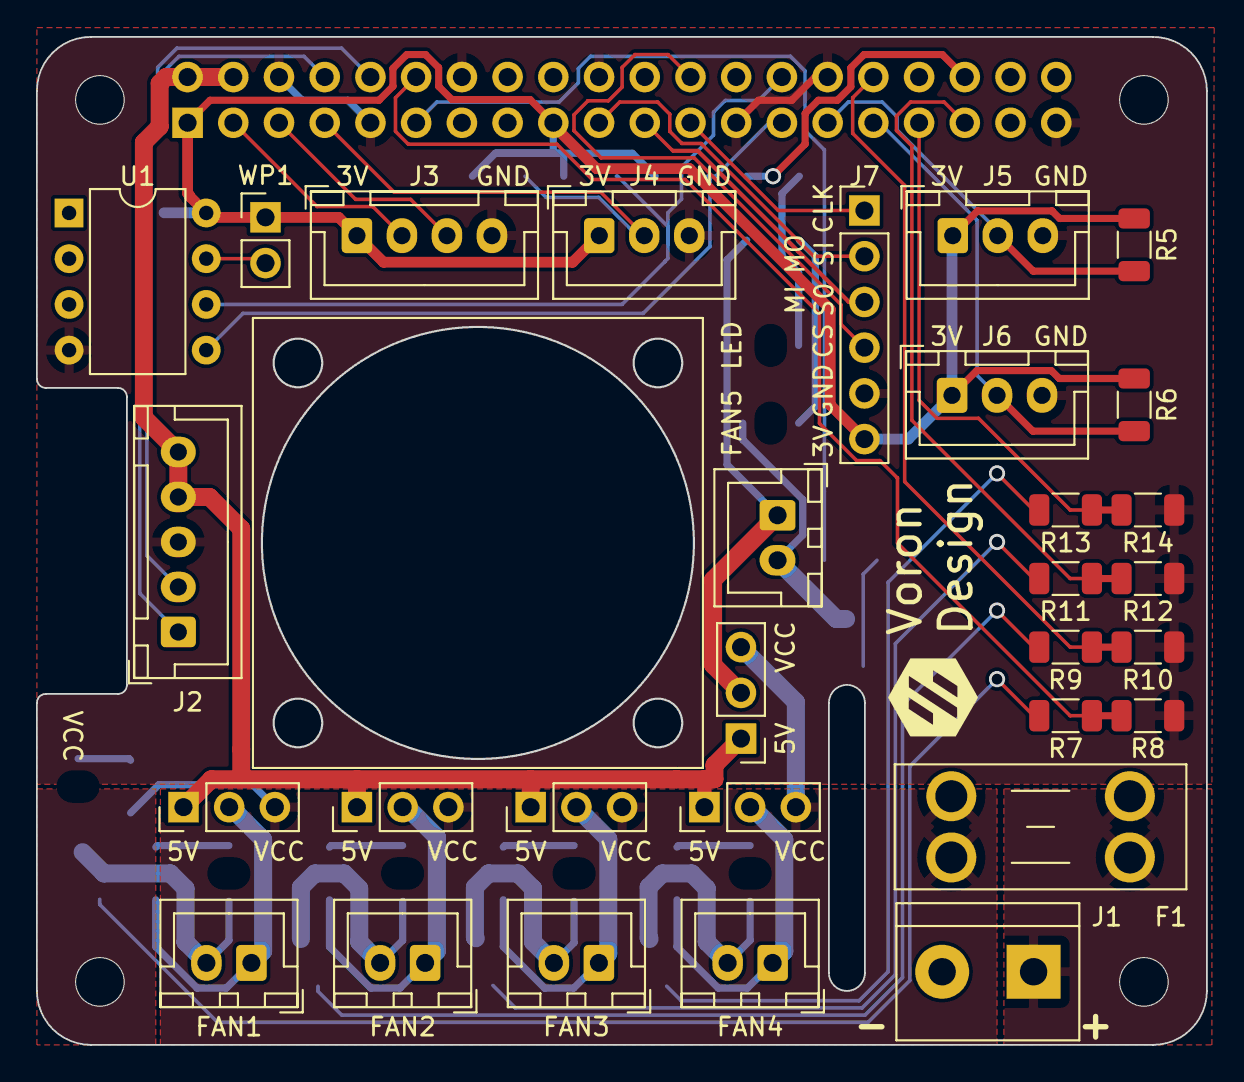
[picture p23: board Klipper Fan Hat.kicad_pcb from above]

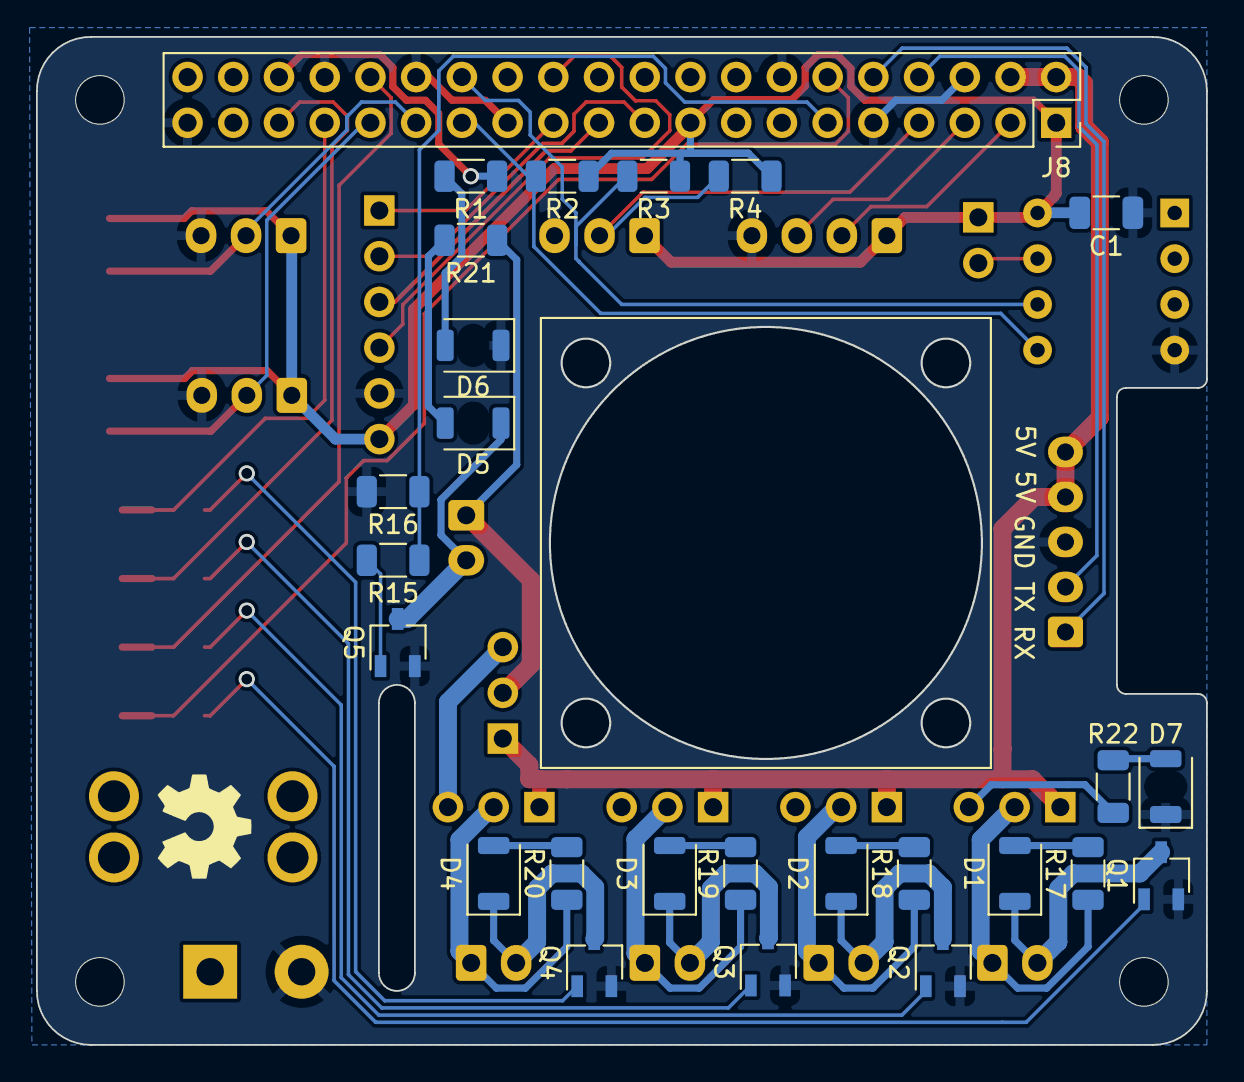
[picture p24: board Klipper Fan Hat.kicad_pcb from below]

Board: 2 copper layers, 65.0 x 56.0 mm, 60 parts (26 on the bottom side), 47 nets.

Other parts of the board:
MH1, MH2, MH3, MH4: MountingHole_2.7mm_M2.5

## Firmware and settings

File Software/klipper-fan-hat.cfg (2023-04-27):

[mcu rpi]
#####################################################################
# Compile the Klipper micro-controller code for "Linux process"
#####################################################################
serial: /tmp/klipper_host_mcu
##--------------------------------------------------------------------

[static_digital_output status_led]
pins: rpi:gpio16

#####################################################################
#      Fans
#####################################################################

# For hardware PWM add one of the following to `/boot/config.txt`:
# dtoverlay=pwm-2chan,pin=18,pin2=19,func=2,func2=2
# dtoverlay=pwm-2chan,pin=12,pin2=13,func=4,func2=4

# add the following to /etc/rc.local before exit 0:
# echo 0 > /sys/class/pwm/pwmchip0/export
# echo 1 > /sys/class/pwm/pwmchip0/export

# Then enable `hardware_pwm` on the selected pins

[fan_generic fan1]
pin: rpi:gpio18
#pin: rpi:pwmchip0/pwm0
hardware_pwm: false

[fan_generic fan2]
pin: rpi:gpio12
#pin: rpi:pwmchip0/pwm0
hardware_pwm: false

[fan_generic fan3]
pin: rpi:gpio19
#pin: rpi:pwmchip0/pwm1
hardware_pwm: false

[fan_generic fan4]
pin: rpi:gpio13
#pin: rpi:pwmchip0/pwm1
hardware_pwm: false

# Control the Pi fan by host temperature
[temperature_fan raspberry_pi]
pin: rpi:gpio17
sensor_type: temperature_host
min_temp: 10
max_temp: 100
target_temp: 35
control: pid
pid_kp: 1.0
pid_ki: 0.5
pid_kd: 2.0

#####################################################################
#      I2C
#####################################################################

# Example1: Using the I2C bus with an OLED Display
#[display]
#lcd_type: sh1106
#i2c_mcu: rpi
#i2c_bus: i2c.1
#x_offset: 1 # Shift the display towards the right
# If not using GPIO pins below you can attach a rotary encoder:
#click_pin: ^!rpi:gpio4
#encoder_pins: ^rpi:gpio5, ^rpi:gpio6

# Example2: Using the I2C bus to read a HTU21D sensor
#[temperature_sensor enclosure_temp]
#sensor_type: HTU21D
#i2c_mcu: rpi
#i2c_bus: i2c.1

#[gcode_macro QUERY_ENCLOSURE]
#gcode:
#    {% set sensor = printer["htu21d enclosure_temp"] %}
#    {action_respond_info(
#        "Temperature: %.2f C\n"
#        "Humidity: %.2f%%" % (
#            sensor.temperature,
#            sensor.humidity))}

#####################################################################
#      1-wire & GPIO
#####################################################################

# GPIO4 is the default pin for 1-Wire sensors
[output_pin gpio4]
pin: rpi:gpio4
value: 0
shutdown_value: 0

# Example1: Using 1-wire DS18B20 temperature sensor
# To enable 1-wire add the following to `/boot/config.txt`:
# dtoverlay=w1-gpio
#[temperature_sensor enclosure_temp]
#sensor_type: DS18B20
#serial_no: 28-031674b175ff # Find with: ls /sys/bus/w1/devices/
#ds18_report_time: 3.0 # Seconds between readings, minimum of 1.0
#sensor_mcu: rpi

[output_pin gpio5]
pin: rpi:gpio5
value: 0
shutdown_value: 0

[output_pin gpio6]
pin: rpi:gpio6
value: 0
shutdown_value: 0

# Example2: Using pin as filament sensor
#[filament_switch_sensor filament_sensor]
#pause_on_runout: true
#switch_pin: ^!rpi:gpio5

#####################################################################
#      SPI
#####################################################################

# Example: Using the SPI bus of the RPi with an AXDL345 Accelerometer
#[adxl345]
#cs_pin: rpi:None

#[resonance_tester]
#accel_chip: adxl345
#probe_points: 150, 150, 20 # an example

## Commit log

2023-03-21 Add Version 1
    [Klipper Expander Hat-B_Cu.gbl, Klipper Expander Hat-B_Mask.gbs, Klipper Expander Hat-B_Silkscreen.gbo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]
2023-03-29 Update product id and version number, and add device tree overlay source file to automatically enable SPI and I2C at the correct baud rate
2023-03-30 Rename to Klipper Fan Hat
    [Klipper Fan Hat-B_Cu.gbl, Klipper Fan Hat-B_Mask.gbs, Klipper Fan Hat-B_Silkscreen.gbo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]
2023-04-21 Update Klipper Fan Hat to V2
    [Klipper Fan Hat-B_Cu.gbl, Klipper Fan Hat-B_Mask.gbs, Klipper Fan Hat-B_Silkscreen.gbo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]
2023-04-26 Update Klipper Fan Hat software to V2
    [Klipper Fan Hat.kicad_pcb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]
2023-04-26 GPIO 16 is used for status LED
2023-04-26 Add version number
    [Klipper Fan Hat.kicad_pcb]
2023-04-27 Update Klipper Config
    [klipper-fan-hat.cfg]
2023-04-28 Add Klipper Setup Documentation and Component Images
2023-04-28 Describe the connectors

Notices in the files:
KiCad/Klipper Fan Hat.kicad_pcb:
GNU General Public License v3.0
